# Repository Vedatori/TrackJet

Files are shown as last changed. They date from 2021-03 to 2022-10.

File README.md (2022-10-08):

# TrackJet (cz)
TrackJet je otevřená platforma robotického vozidla vyvinutá pro [Robotický tábor 2021](http://wp.vedatori.com/pobytove-tabory/) organizovaný spolkem [Vědátoři](http://wp.vedatori.com/). Jedná se o nástupní verzi vozidla [TrackRay](https://github.com/vedatori/TrackRay), ve které byly vylepšeny jeho terénní schopnosti a přidány nové funkcionality. Byla redesignována mehanická konstrukce i řídicí elektronika, pro kterou byl vyvinut odpovídající software. 

Hlavní mechanickou částí je 3D tištěné šasi, které je doplněno dalšími 3D tištěnými díly. Plošné díly jsou laserem vyřezány z překližky. Spojování je prováděno především šrouby M3. Je použito minimum lepených spojů tak, aby bylo možné vrátit jakýkoliv krok při stavbě. Obsahuje zadní pohonná kola a na každé straně dále tři kola pro vedení pásu. Všechna kola jsou uložena pevně. Pásy jsou vytištěny na 3D tiskárně tak, aby se již při tisku vytvořilo kloubové spojení jednotlivých segmentů, což vede ke snížení času potřebného pro stavbu.

Veškerá elektronika je umístěna na jedné DPS. Ze spodní strany je připevněn zdroj energie - akumulátor 18650. Jeho nabíjení je řešeno na DPS, pro nabití není nutné ho vyjmout. Robota řídí ESP32 připájené přímo do DPS. Pro orientaci v prostoru robot využívá snímání pohybu pásů pomocí optických enkodérů a senzoru LiDAR umístěného na otočné konzoli. Vstupy od uživatele je možné zadat pomocí rotačního enkodéru, potenciometru a tlačítka, výstupy jsou zobrazeny na LED matici, bzučákem nebo jiných LED. Programování a nabíjení robota je prováděno přes USB-C.

Software je připraven na výuku programování. Tomu je přizpůsobena knihovna, pomocí které uživatelé jednoduše ovládají periferie robota bez nutnosti nízkoúrovňového programování jednotlivých částí. Pro výuku programování je připraven také návod popisující jednotlivé funkce a příklady jejich použití. Vše bylo navrženo s důrazem na rozvoj schopností algoritmizace a programování účastníků.
Součástí softwarového balíku je i kompletní program pro dálkové ovládání přes WiFi. Vozidlo umožňuje komunikaci jak přes vlastní WiFi, tak přihlášení k již existující síti. To mu umožňuje jízdu i v širém prostoru. TrackJet můžete vidět v akci v [tomto videu](https://www.youtube.com/watch?v=zHig3jCnhBY).

Při stavbě TrackJet postupujte podle připravených návodů v následujícím pořadí:
1. [Návod pro mechaniku](https://github.com/vedatori/TrackJet/blob/main/Manuals/TrackJet_mechanics_cz.md)
1. [Návod pro elektroniku](https://github.com/vedatori/TrackJet/blob/main/Manuals/TrackJet_electronics_cz.md)
1. [Návod pro programování](https://github.com/vedatori/TrackJet/blob/main/Manuals/TrackJet_programming_cz.md)

## Licence
* Obsah tohoto repozitáře mimo složku *Software* je sdílen pod licencí [Attribution-NonCommercial-ShareAlike 4.0 International (CC BY-NC-SA 4.0)](https://creativecommons.org/licenses/by-nc-sa/4.0/).
* Obsah složky *Software* je sdílen pod licencí [GNU Lesser General Public License v3.0](https://www.gnu.org/licenses/lgpl-3.0.en.html).

# TrackJet (en)

TrackJet is an open-source robotic vehicle platform developed for the [Robotic camp 2021 (cz)](http://wp.vedatori.com/pobytove-tabory/) organized by [Vědátoři (cz)](http://wp.vedatori.com/) society. It is a succesor of [TrackRay](https://github.com/vedatori/TrackRay) robotic vehicle. TrackJet introduces enhanced terrain abilities and new functionalities. Mechanical parts, electronics and software were redesigned.

TrackJet consists of a main 3D printed part - chassis, several other 3D printed parts and laser cut plywood parts. M3 bolts are used in the assembly process, which grants the possibility to undo every step in case of assembly error. Rear propulsion wheel and three guiding wheels are placed on every side of the vehicle. Tracks are designed to be 3D printed in one piece with joints between segments which minimizes assembly time.

All electronic components are placed on a single PCB. This board contains 18650 battery and a charger circuit. Therefore, it is not needed to take the battery out in order to charge it. ESP32 soldered to the PCB is used for peripherals control and WiFi connectivity. TrackJet finds its orientation in space using LiDAR sensor and optical encoders. User inputs can be made using rotary encoder, potentiometer and a button. LED matrix, buzzer and other LEDs are used for communication with user. Vehicle is programmed and charged via USB-C.

Electronics and software is designed for programming education. TrackJet contains a library which allows easy peripherals control without the need of low-level programming abilities. Repository contains programming manual (in czcech language) with description of commands and examples. WiFi remote control is a part of the software pack in this repository. ESP32 can be connected to external WiFi or it can create its own network so it is possible to drive outdoors without network coverage. You can see TrackJet in action in [this video](https://www.youtube.com/watch?v=zHig3jCnhBY).

In the build of the TrackJet proceed according to the prepared manuals in the following order:
1. [Mechanics manual](https://github.com/vedatori/TrackJet/blob/main/Manuals/TrackJet_mechanics_cz.md)
1. [Electronics manual](https://github.com/vedatori/TrackJet/blob/main/Manuals/TrackJet_electronics_cz.md)
1. [Programming manual](https://github.com/vedatori/TrackJet/blob/main/Manuals/TrackJet_programming_cz.md)

## License
* The contents of this repository excluding folder *Software* is shared under license [Attribution-NonCommercial-ShareAlike 4.0 International (CC BY-NC-SA 4.0)](https://creativecommons.org/licenses/by-nc-sa/4.0/).
* The contents of the folder *Software* is shared under license [GNU Lesser General Public License v3.0](https://www.gnu.org/licenses/lgpl-3.0.en.html).


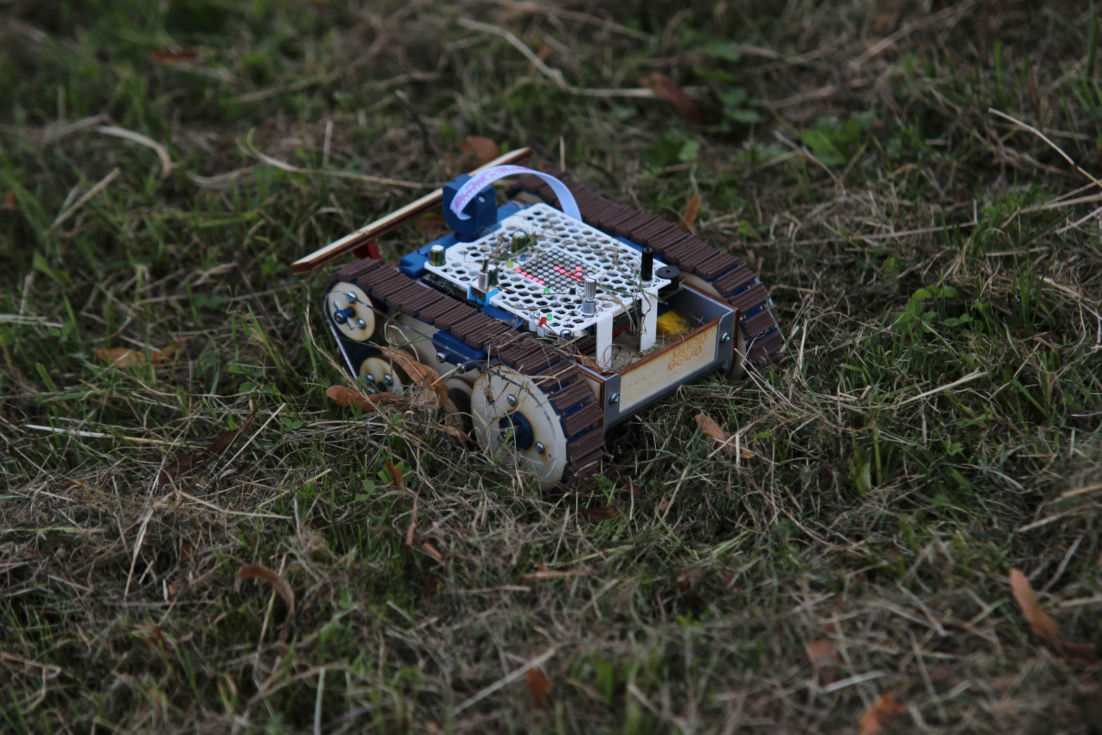
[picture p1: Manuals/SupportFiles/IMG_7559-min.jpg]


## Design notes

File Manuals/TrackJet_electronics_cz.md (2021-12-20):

V tomto dokumentu je uveden návod na osazení desky plošných spojů. Některé součástky byly osazeny strojově při výrobě desek. Zbytek osazení je předmětem tohoto návodu.
Pro tento návod si uvedeme následující pojmy: 
* DPS (Deska Plošných Spojů) - Placatá věc, na kterou budeme nyní pájet součástky a které jsou skrze ni elektricky pospojované.
* PCB (Printed Circuit Board) - To stejné, co DPS.
* SMD (Surface Mount Device) - Tzv. bezvývodové elektronické součástky, které mají krátké nožičky. Tyto součástky jsou připájeny k DPS pouze z jedné strany. Tyto součástky byly osazevy strojově při výrobě DPS.
* THT (Through-hole Technology) - Tzv. vývodové elekotronické součástky, které mají dlouhé nožičky. Tyto nožičky jsou před zapájením součástky prostrčeny skrz díry v DPS.

THT součástky budeme v následujících krocích pájet následujícím způsobem:
1. Součástku vkládáme ze strany, kde je naznačena silkscreenem (kde je bílou barvou natištěn její obrys).
1. Součástku přitlačíme až k desce nebo co nejblíž.
1. Součástku pájíme ze strany, na kterou trčí vývody.
1. Vývody po zapájení zastřihneme.

# Obsah
* [Pájení senzorů pohybu](#LED1)
* [Pájení LED](#LED2)
* [Pájení malých součástek](#male)
* [Pájení větších součástek](#vetsi)
* [Pájení konektorů a senzorů čáry](#konektory)
* [Zakrytování PCB, propojení periferií](#finalizace1)
* [LIDAR](#finalizace2)
* [LIDAR2](#finalizace3)

## <a name = LED1>Pájení senzorů pohybu</a>
**Potřebujeme:**
* kleště
* 4x modul s LED a fotodiodou
* 2x plastový držák pro modul z 3D tiskárny
* 2x plastový vymezovač z 3D tiskárny
* 2x šroub M3x8 

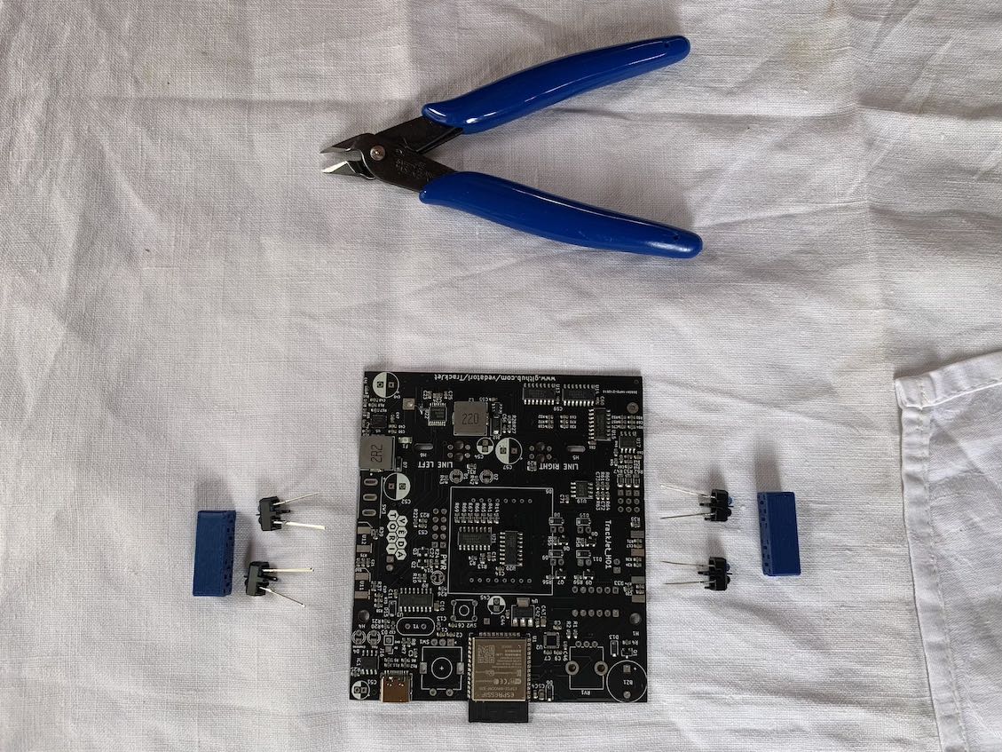
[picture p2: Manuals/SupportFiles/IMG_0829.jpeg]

**Postup:**
1. Vložte postupně moduly do držáku z 3D tiskárny. *Je třeba dodržet orientaci diod s obrázkem pro jednotlivé strany. Modrá čára na schématu označuje pozici "nosu" na součástce.* Barvu diod je možné rozpoznat pod světlem např. z LED telefonu.
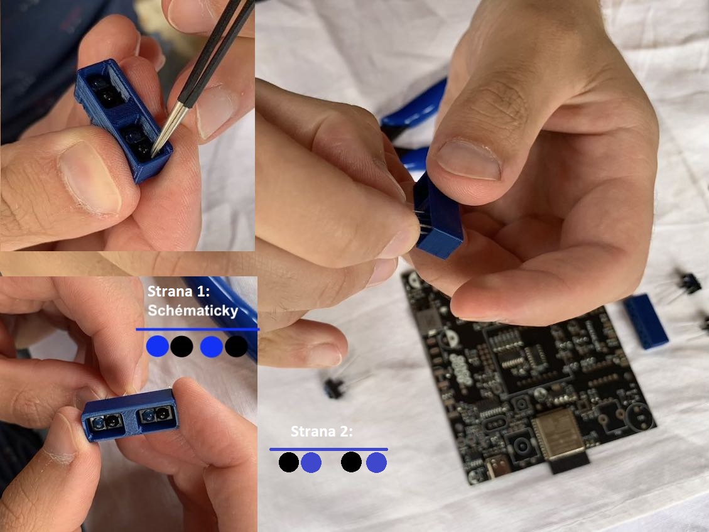
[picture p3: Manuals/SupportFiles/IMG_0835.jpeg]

1. Vývody musí být protažené dvěma podélnýma dírama v 3D tisknutém díle (ne těmi v rozích).
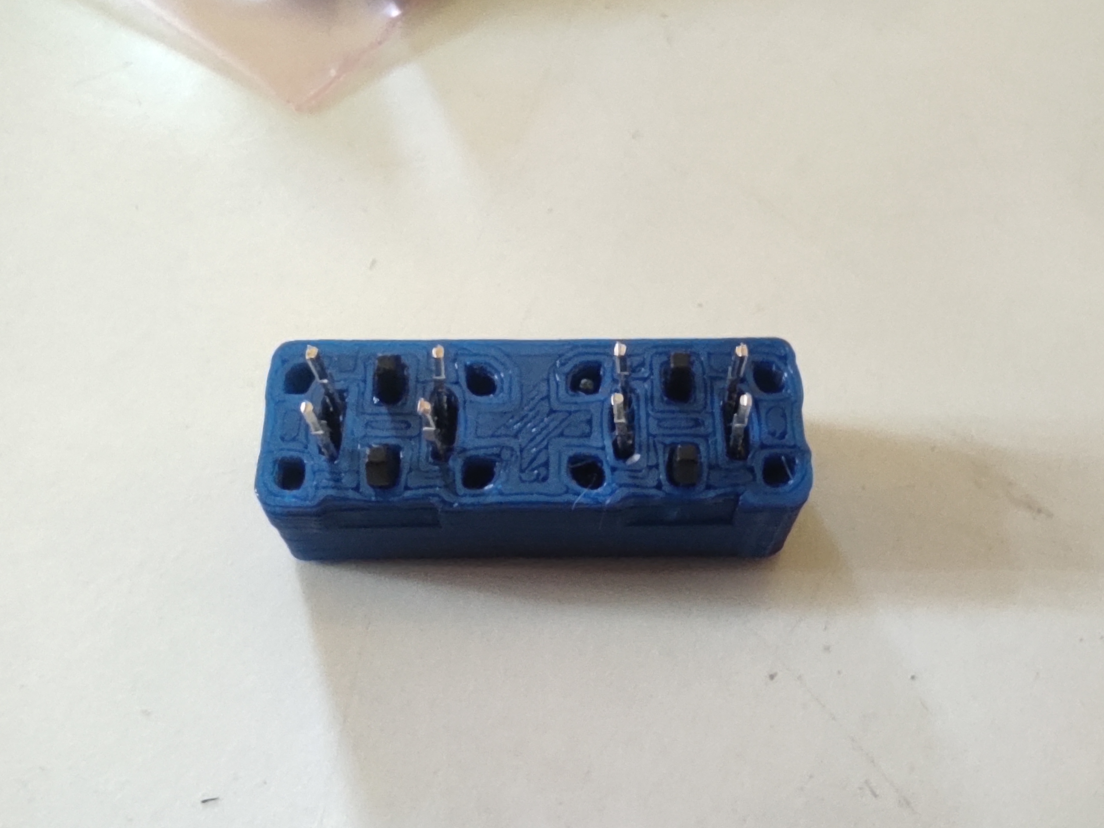
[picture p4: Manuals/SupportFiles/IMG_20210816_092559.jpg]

1. Opakujte postup pro druhou stranu 2 podle schématu. Zarovnejte nožičky podle obrázku, aby obejmuly shora a zespodu PCB a směřovali doprostřed pájecí plochy. *Nos na součástce je nahoře.*
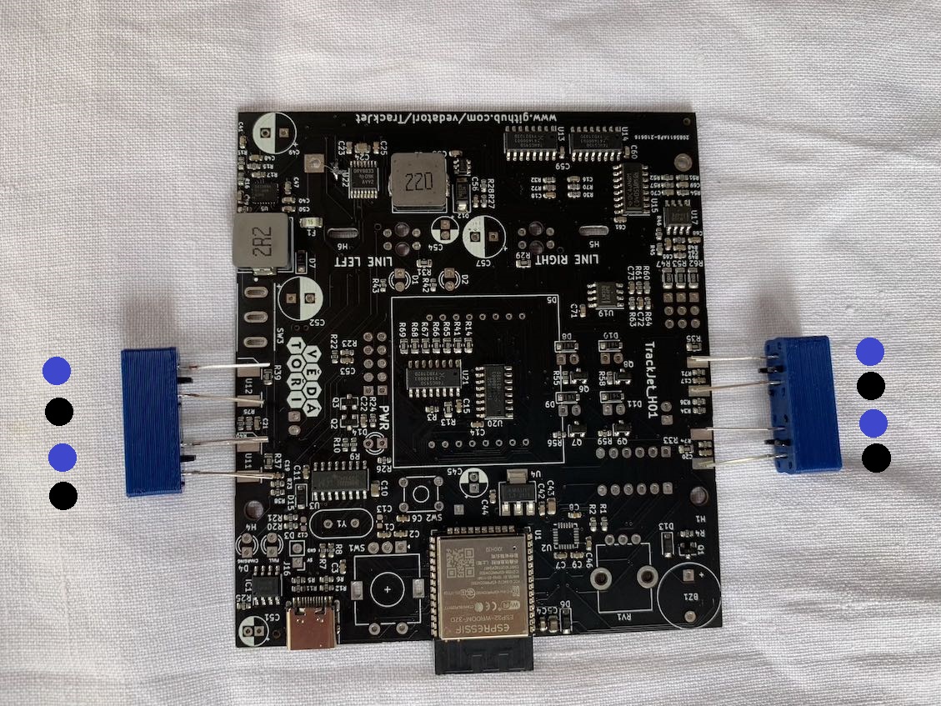
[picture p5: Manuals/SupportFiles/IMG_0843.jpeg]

1. Použijte zarovnávací nástroj z 3D tiskárny, umístěte do něj moduly podle obrázku. Na vyznačené červené čáře zakraťte vývody kleštěmi.
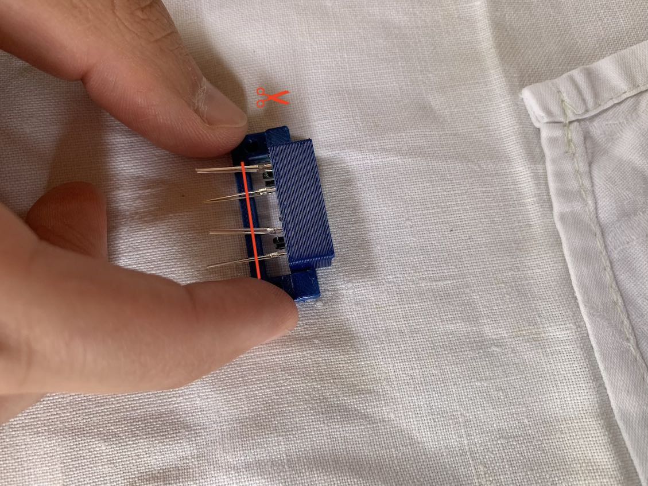
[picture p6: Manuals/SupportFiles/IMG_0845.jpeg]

1. Zarovnávací nástroj z 3D tiskárny umístěte pod PCB a přišroubujte šroubkem.
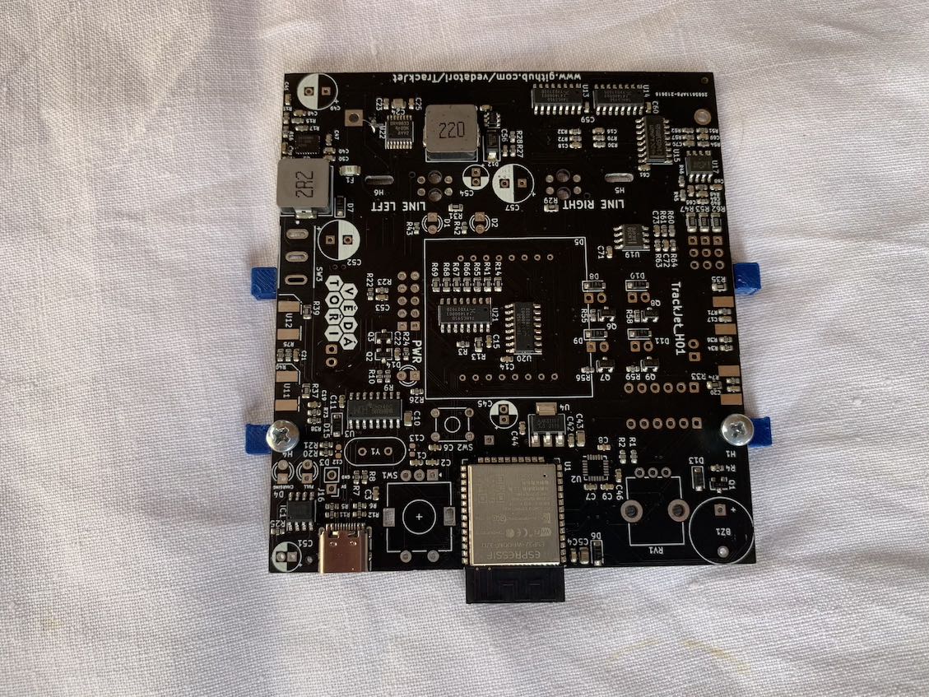
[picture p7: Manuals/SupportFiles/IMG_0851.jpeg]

1. Zarovnejte nožičky podle obrázku, aby obejmuly shora a zespodu PCB a směřovaly doprostřed pájecí plochy. *Modul z 3D tiskárny musí přiléhat k PCB bez mezery.*
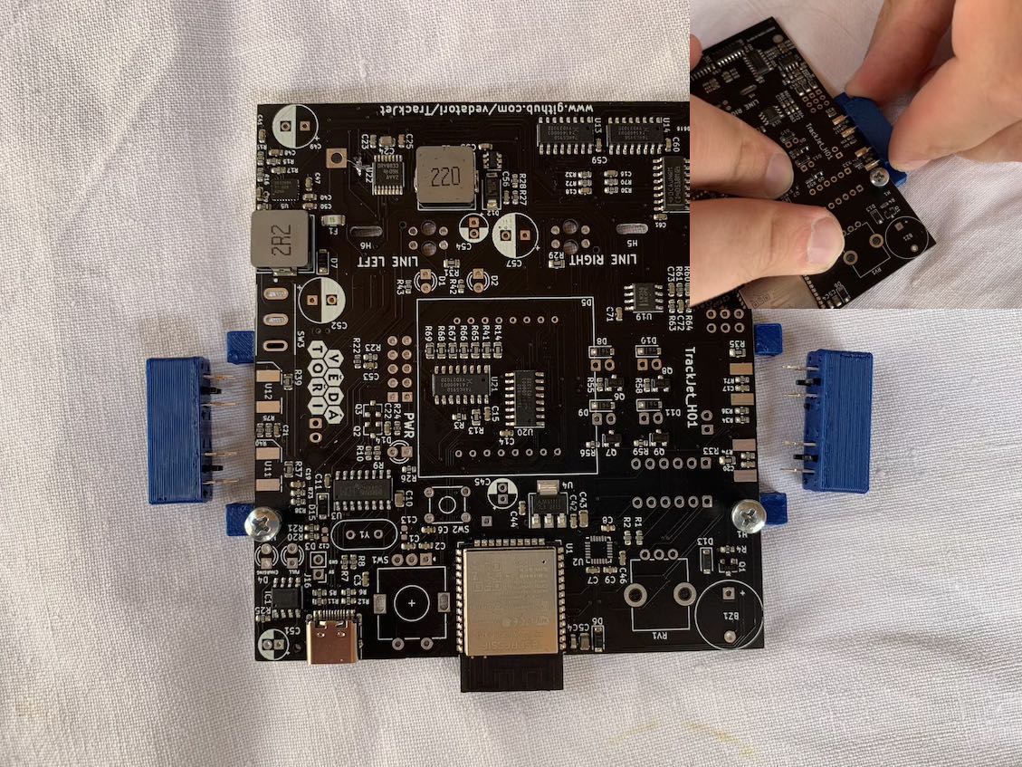
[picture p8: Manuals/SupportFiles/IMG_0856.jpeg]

1. *Zapájejte z horní strany PCB.*
1. Vyšroubujte díl pro zarovnání z 3D tiskárny. 
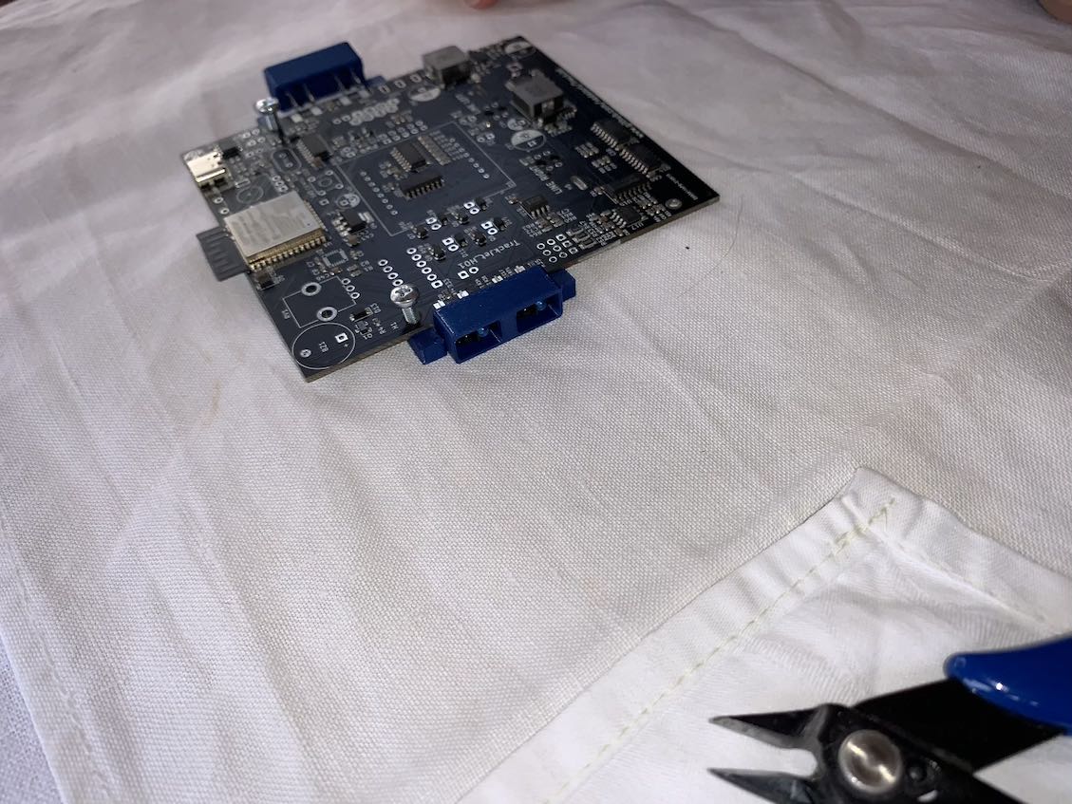
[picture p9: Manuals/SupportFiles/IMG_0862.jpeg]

1. Otočte na druhou stranu, vyrovnejte nožičky na střed pájecí plochy. Zapájejte.
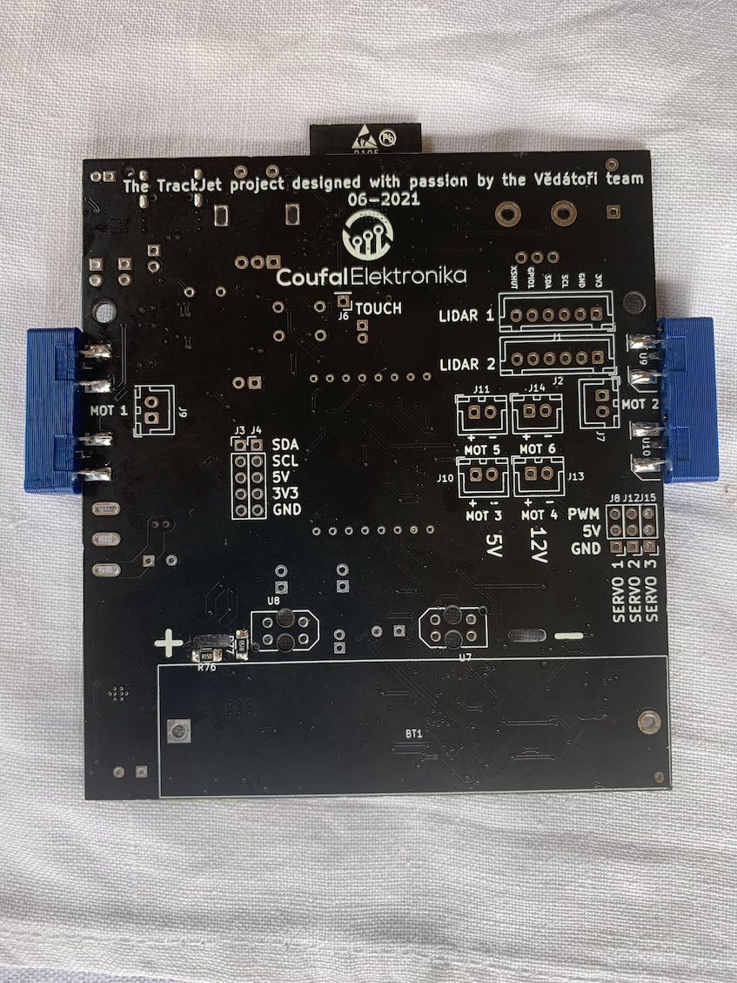
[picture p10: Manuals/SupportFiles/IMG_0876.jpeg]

1. Otestujte, zda PCB padne do šasi. *Při usazování netlačte. Pokud deska nezapadne hladce, zavolejte vedoucího.*
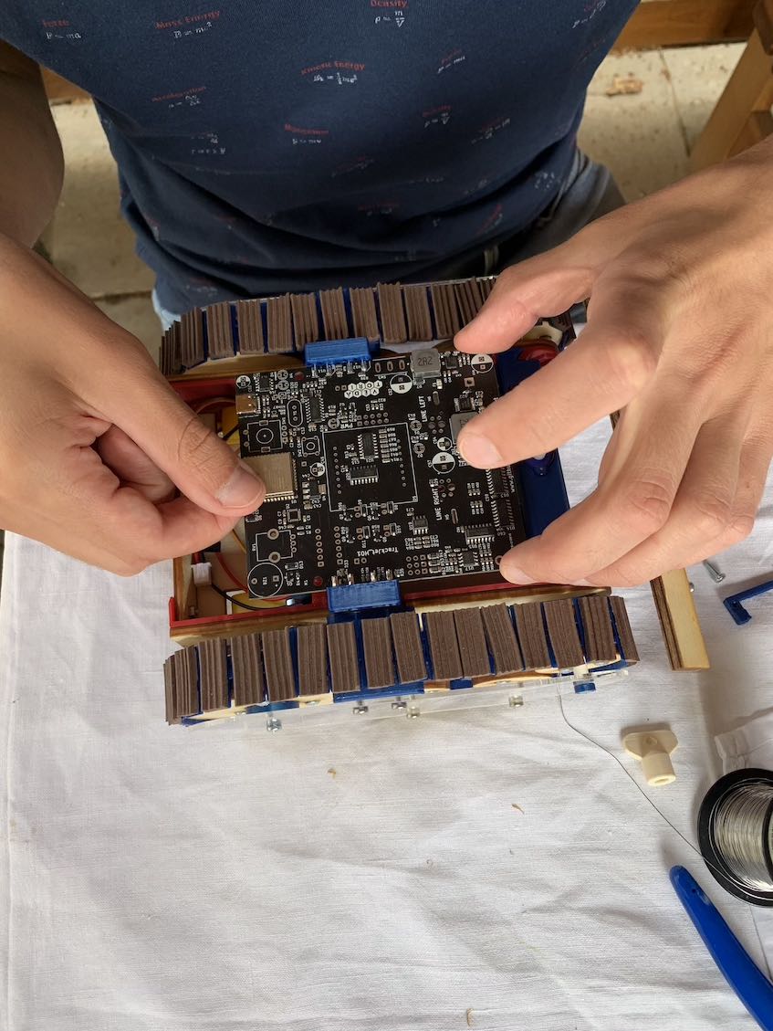
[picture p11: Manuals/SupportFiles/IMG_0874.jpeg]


## <a name = LED2>Pájení LED</a>
**Potřebujeme:**
* kleště
* 2x zelená LED
* 1x červená LED
* 2x LED oblíbené barvy vlastního výběru
* 5x distanční sloupek pro LED

**Postup:**
<span style="color: red;">**POZOR: LED mají definovanou polaritu!**</span> U každé LED zkontrolujte, že kratší nožku vsouváte do čtveraté díry! 
1. Na každou LED navlékněte distanční sloupek. Použijte ty bílé, které máte v sáčku s mechanikou
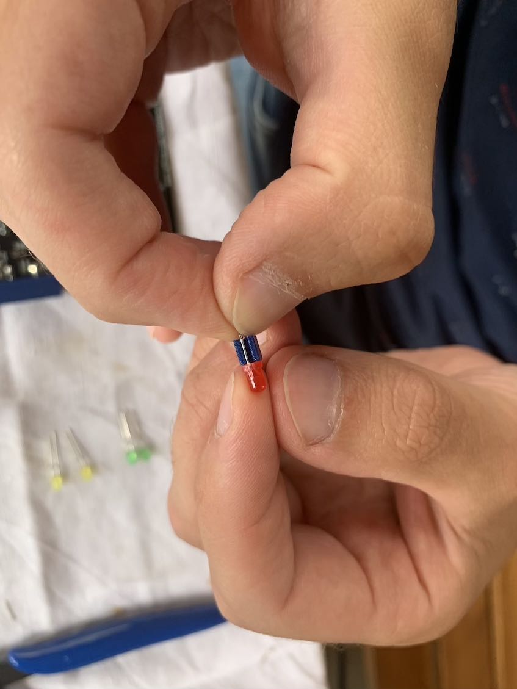
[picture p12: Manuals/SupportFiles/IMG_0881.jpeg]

1. Provlékněte červenou LED místem označeným D4 CHARGING. Zahněte nožičky natěsno u PCB. Cín se nanáší ze strany s logem Coufal Elektronika. Zapájejte.
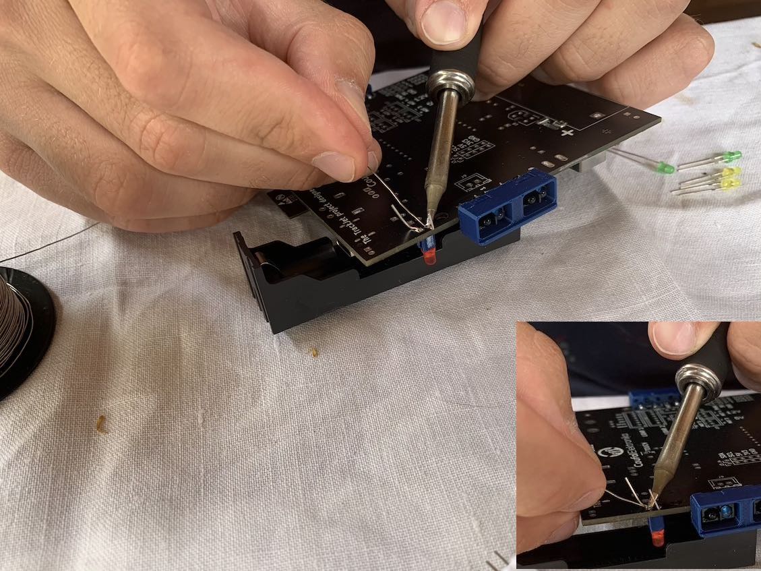
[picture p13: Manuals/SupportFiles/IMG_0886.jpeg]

1. Provlékněte zelenou LED místem označeným D3 FULL. Opakujte stejný postup pájení jako v předchozím kroku.
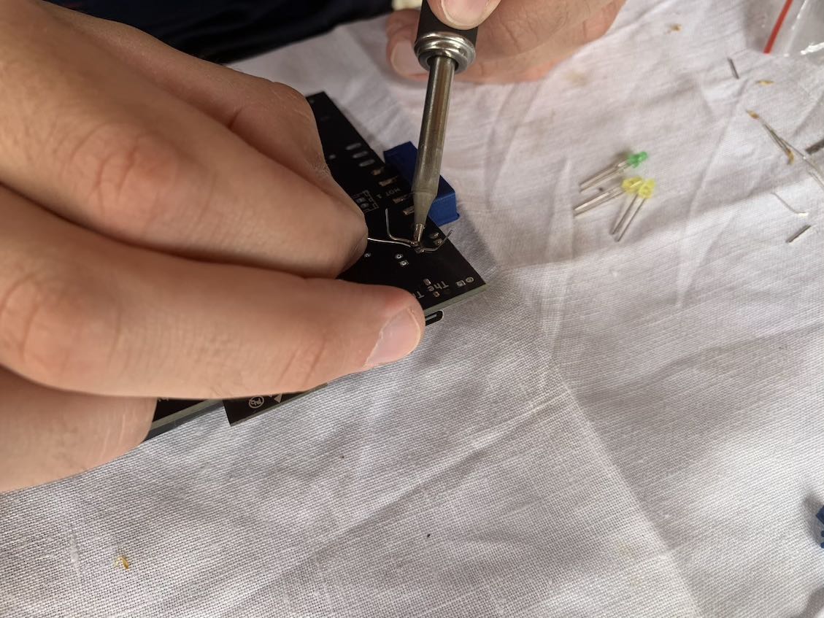
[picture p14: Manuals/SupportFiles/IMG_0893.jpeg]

1. Zastřihněte nožičky u PCB. *Stříhanou nožičku držte rukou, aby neodletěla sousedovi do oka.*
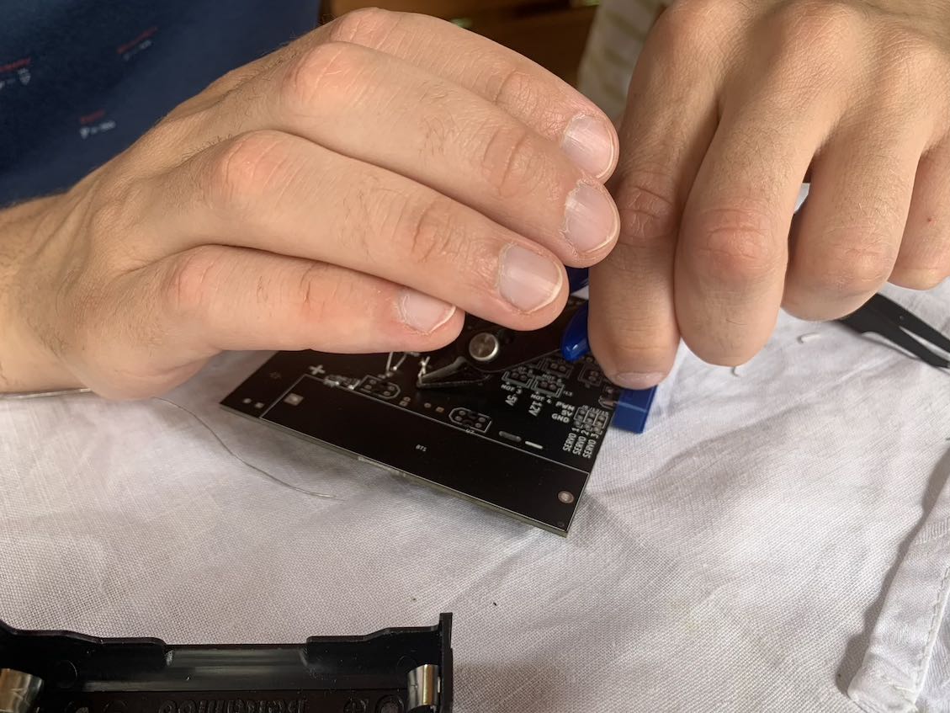
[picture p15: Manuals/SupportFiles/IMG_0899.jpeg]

1. Obdobným postupem zapájejte zelenou LED místem ozančeným D14 a vybrané LED místy označenými D1 a D2.


## <a name = male>Pájení malých součástek</a>
**Potřebujeme:**
* kleště
* bzučák
* 3x elektrolytický kondenzátor 100 µF (menší pouzdro)
* 3x elektrolytický kondenzátor 1000 µF (větší pouzdro)

**Postup:** 
1. Zapájejte buzzer do levého horního rohu. Pozor na polaritu, delší vývod (u symbolu plus na plastovém pouzdře buzzeru) musí být umístěn do otvoru označeným symbolem +. Buzzer mírně nesedí tak, jak by měl, proto je potřeba jeho vývody mírně rozevřít od sebe.
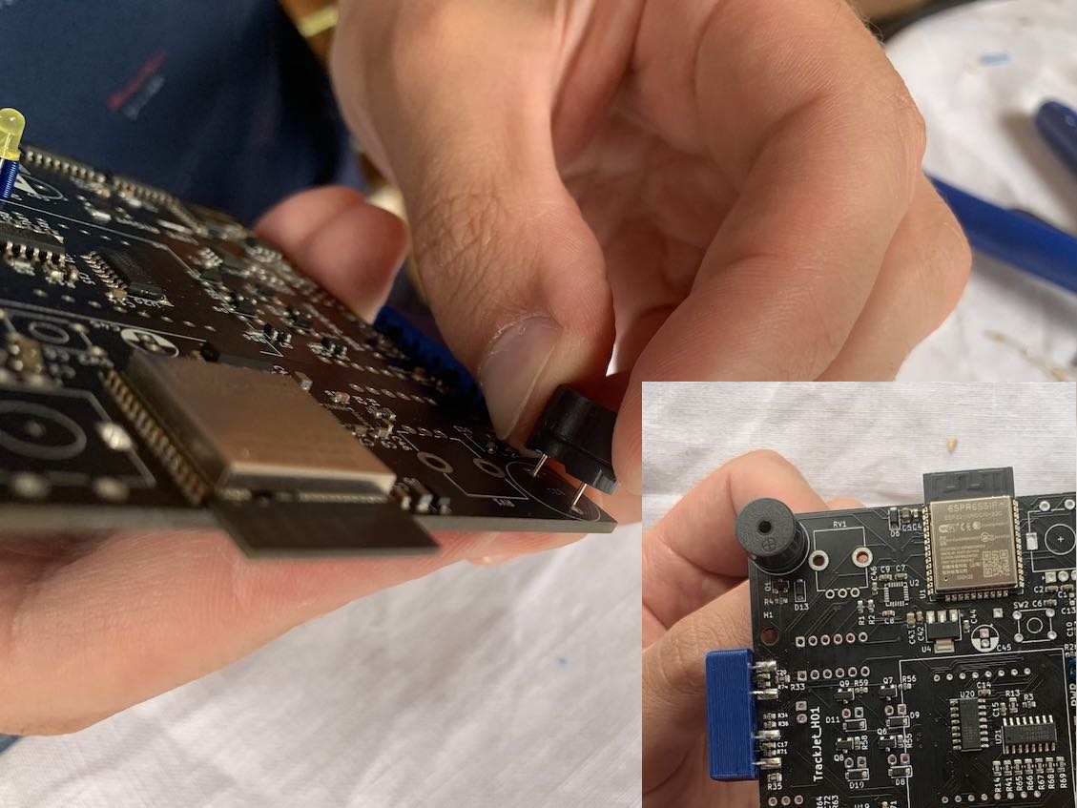
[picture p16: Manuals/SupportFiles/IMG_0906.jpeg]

1. Na místa označená C51, C54 a C45 zapájejte elektolytické kondenzátory 100 µF. Pozor na polaritu, delší vývod musí směřovat do otvoru, u kterého je smybol + a jeho okolí není zabarvené bílou barvou. 
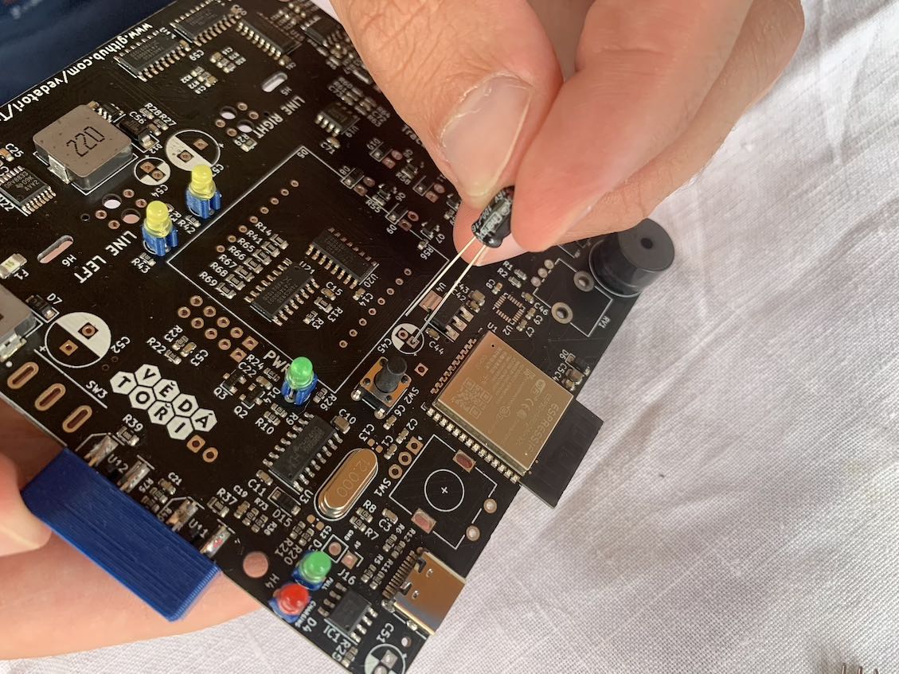
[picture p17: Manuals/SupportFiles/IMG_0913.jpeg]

1. Na místa označená C49, C52 a C57 zapájejte elektolytické kondenzátory 1000 µF. Pozor na polaritu, delší vývod musí směřovat do otvoru, u kterého je smybol + a jeho okolí není zabarvené bílou barvou. 
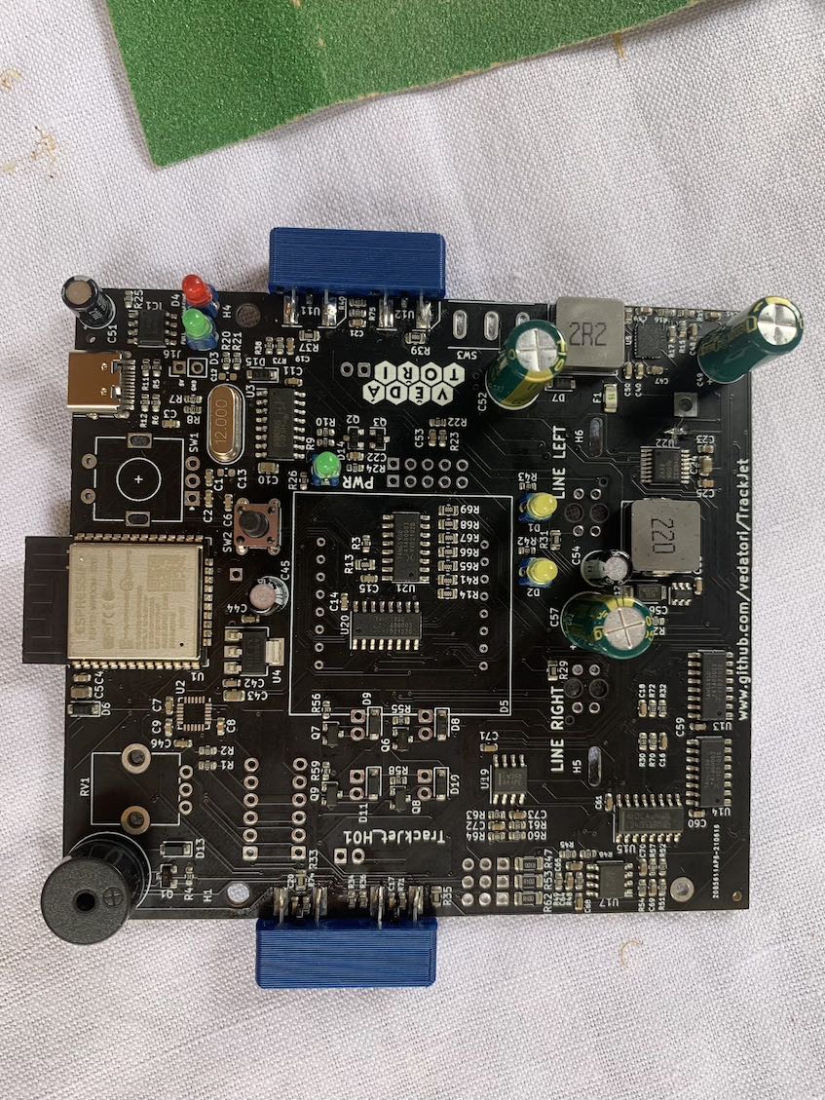
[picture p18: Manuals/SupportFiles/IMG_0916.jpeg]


## <a name = vetsi>Pájení větších součástek</a>
**Potřebujeme:**
* kleště
* přepnínač
* rotační enkodér
* ponteciometr
* matice LED
* tlačítko

**Postup:** 
1. Zapájejte přepínač na místo označené SW3.
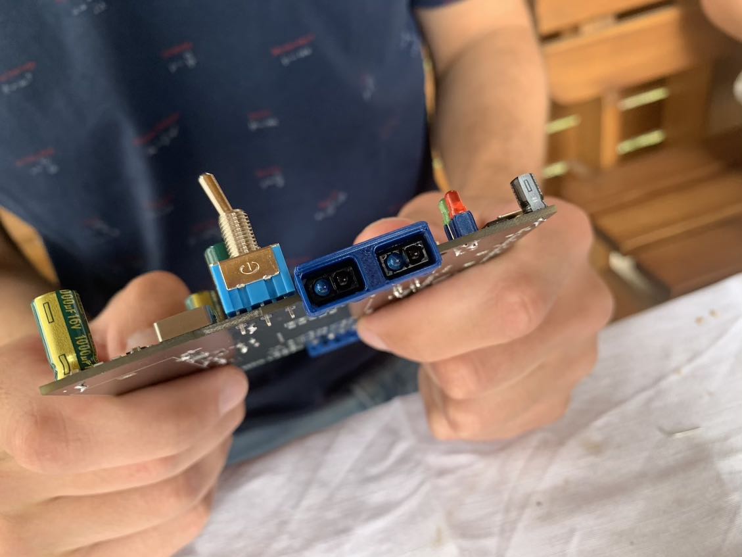
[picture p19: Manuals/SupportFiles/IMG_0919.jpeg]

1. Zapájejte enkodér na místo označené SW1. *Nejprve připájejte kontakty po bocích, poté 3 vývody ze spodní strany. Zkontrolujte, že je enkodér přitlačený k desce a osa čouhá kolmo na desku.*
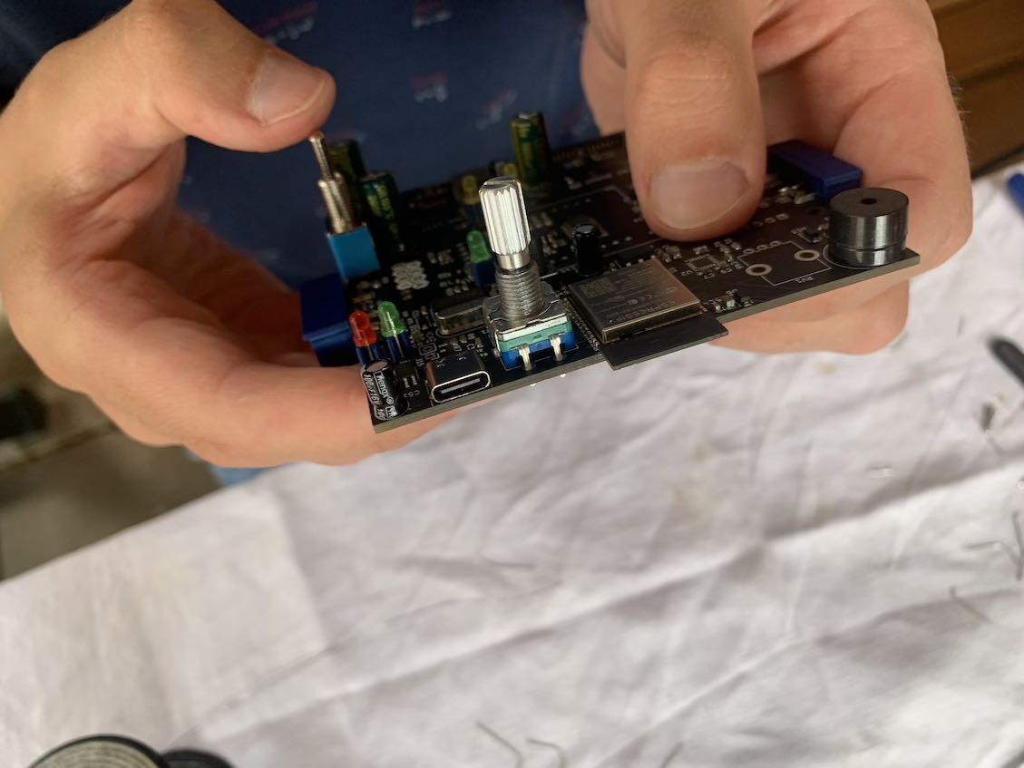
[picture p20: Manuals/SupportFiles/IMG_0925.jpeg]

1. Zapájejte potenciometr na místo označené RV1. *Nejprve připájejte kontakty po bocích, poté 3 vývody ze spodní strany. Zkontrolujte, že je potenciometr přitlačený k desce a osa čouhá kolmo na desku.*
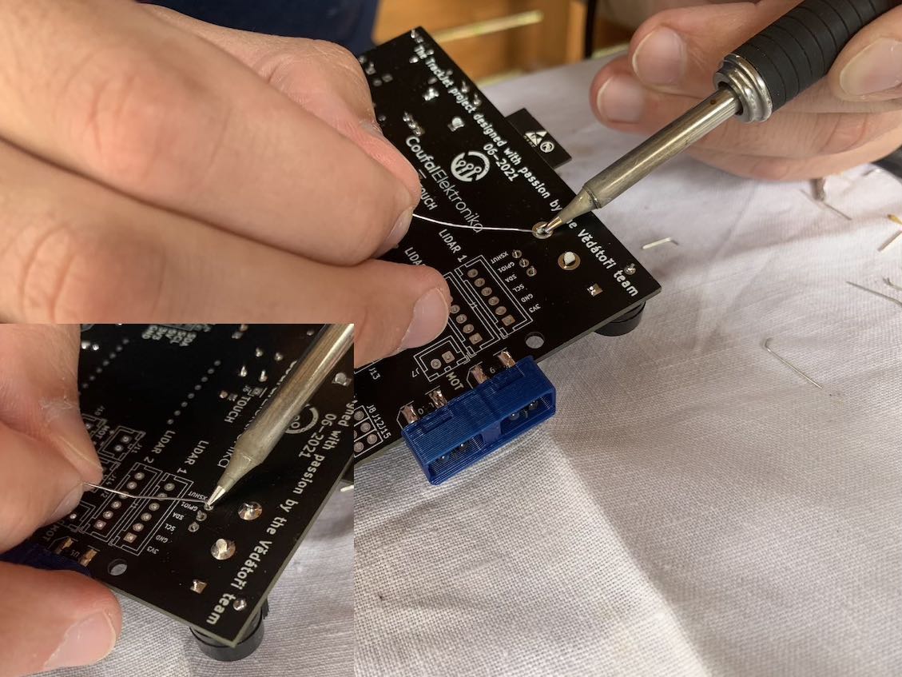
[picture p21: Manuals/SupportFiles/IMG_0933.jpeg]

1. Vložte matici LEDek do PCB. Kód na horní straně musí být blíž k čipu s nápisem Espressif, aby byla zachována polarita, viz obrázek.
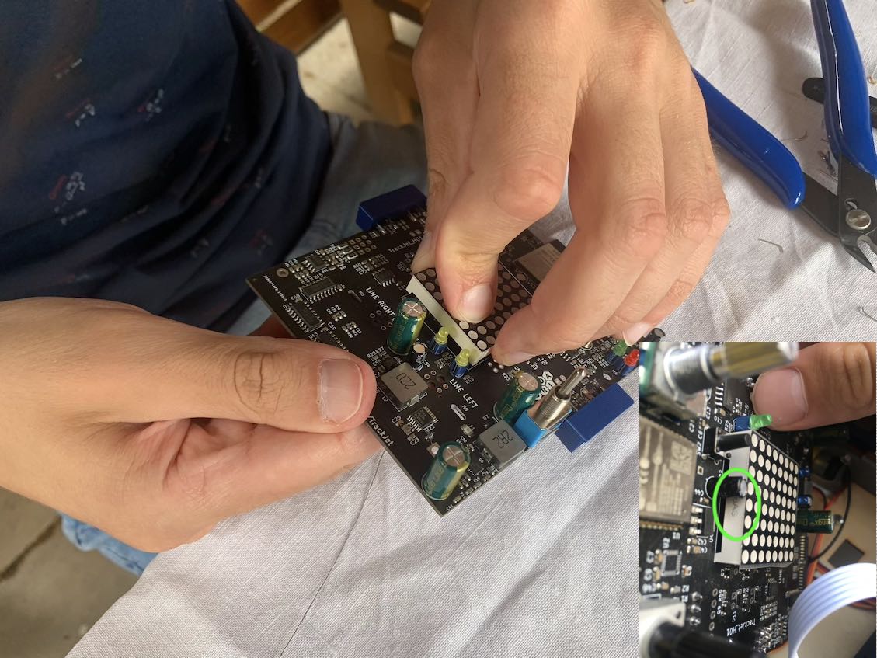
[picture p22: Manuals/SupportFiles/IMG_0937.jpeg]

1. Zahněte pomocí kleští krajní nožičky, aby matice nevypadávala při pájení z desky. Zavolejte vedoucího na kontrolu polarity, oprava špatně otočeného matrixu je téměř neproveditelná!
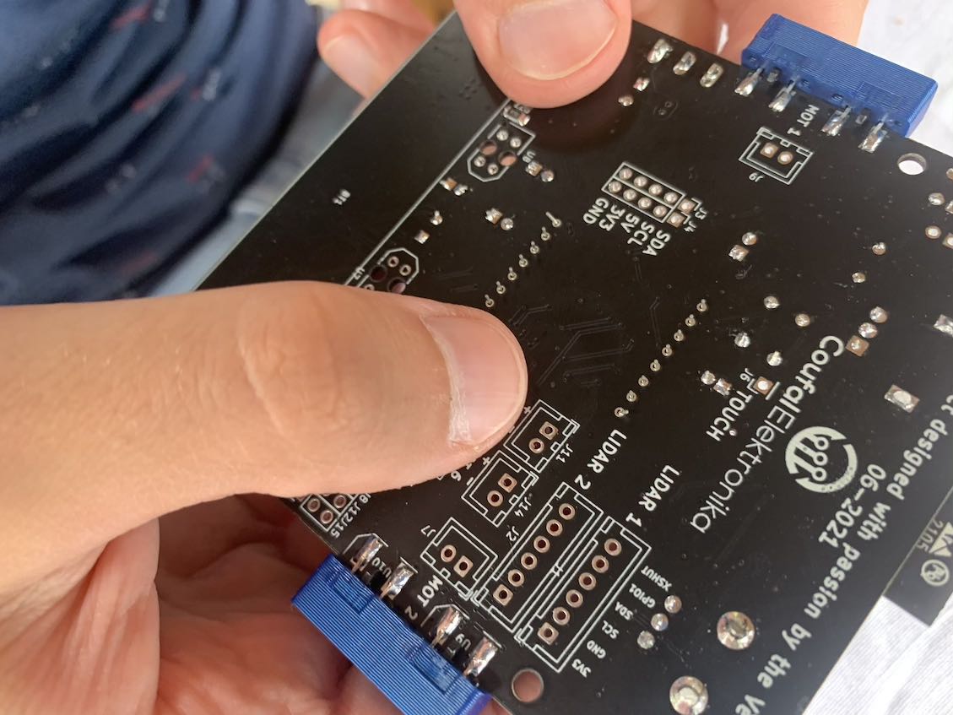
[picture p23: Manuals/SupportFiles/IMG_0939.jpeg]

1. Zapájejte matici LEDek. Na závěr zapájejte tlačítko do místa označeného SW2.
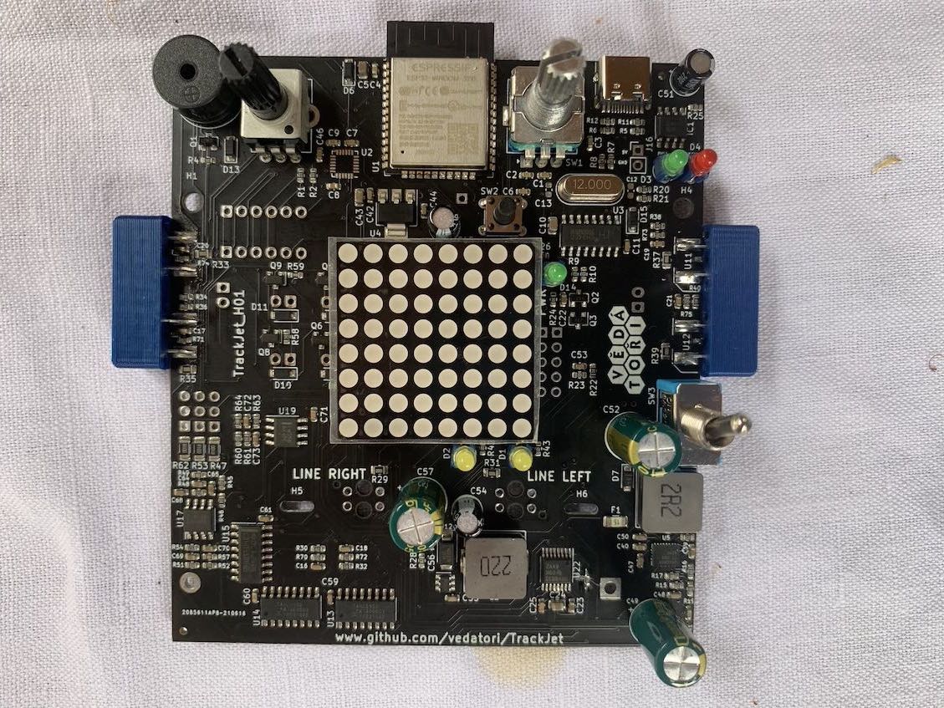
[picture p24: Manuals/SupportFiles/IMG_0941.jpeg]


## <a name = konektory>Pájení konektorů a senzorů čáry</a>
**Potřebujeme:**
* kleště
* 2x konektor se 2 piny
* 1x konektor se 6 piny
* 3x kolíková lišta se třemi konektory
* 2x modul s diodami
* 2x podpěry modulu s diodami z 3D tiskárny
* držák baterie

**Postup:** 
1. Zapájejte kolíkové lišty do míst označených SERVO 1, SERVO 2, SERVO 3. Vytvořte libovolnou barevnou kombinaci. *Kolíková lišta musí být vždy rovnoběžně s nápisy SERVO.*
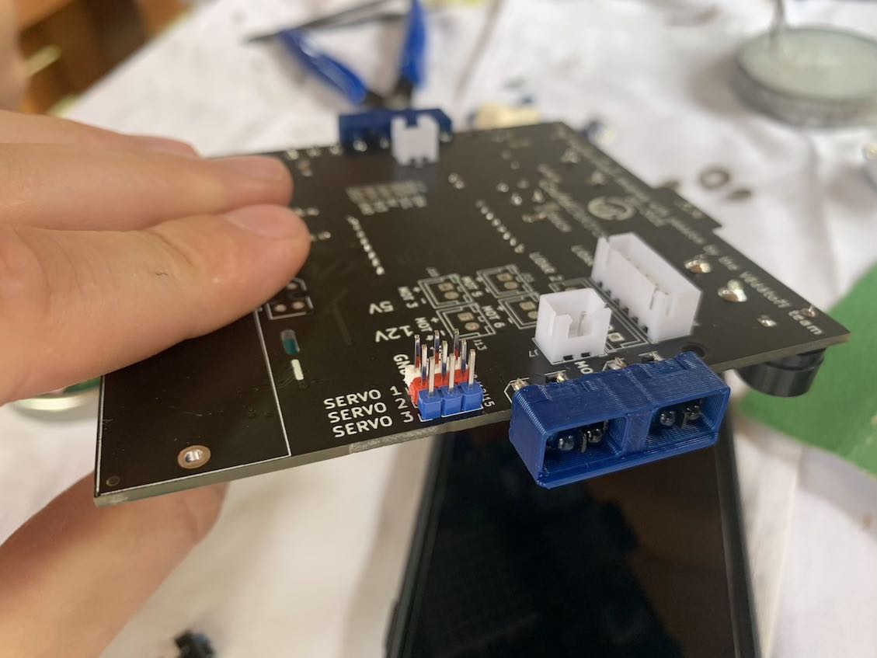
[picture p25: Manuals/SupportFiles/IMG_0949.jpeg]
 
1. Zapájejte lišty konektorů do míst LIDAR1, J6 a J7. Polarita je vždy zřejmá z nákresu na PCB.

1. Provlečete modul s diodami podpěrou. *Veškerá zkosení modulu jsou i na podpěře a musí lícovat. Z jedné strany podpěry je výřez pro kolík vystupující ze součástky.*

1. Připájejte moduly s podpěrou na místa označená U7 a U8. Polarita je zřejmá z nákresu na PCB.

1. Zapájejte držák baterie. Důsledně zkontrolujte polaritu.

1. Překontrolujte desku zepředu.

1. Překontrolujte desku zezadu.


**Nechte desku překontrolovat vedoucím. Nechte si od něj vložit baterku.**

## <a name = finalizace1>Zakrytování PCB, propojení periferií</a>
**Potřebujeme:**
* kryt desky z 3D tiskárny ve tvaru plástve
* 2x stahovací páska
* oboustranná lepicí páska
* kleště

**Postup:**
1. Přichyťte baterku a kryt k PCB pomocí velkých upínacích pásků (volitelné), jejich konce zastřihněte kleštěmi. Pásky protahujte díryami H5 a H6 v desce. Hlavy upínacích pásků dejte do stejné pozice, jako vidíte na obrázku.


1. Konce pásků zastřihněte kleštěmi.

1. Konce pásků zastřihněte kleštěmi.

1. Vystřihněte kousek oboustranné lepicí pásky. Vlepte jej do prostoru mezi otvory pro senzory čáry.

1. Zachyťe kabely od servomotorů na pásku.

1. Zastrčte konektory motoru do desky, jak je naznačeno na obrázku.

1. Připojte vývody od servo motoru na kolíkovou lištu. Výstup SERVO 1 je určen pro radlici. Výstup SERVO 2 je určen pro LIDAR.


## <a name = finalizace2>LIDAR</a>
**Potřebujeme:**
* LIDAR



**Postup:**
1. Připojte vývod LIDARu na konektor LIDAR. Kabel proveďte okolo PCB stejně jako na obrázku.

1. Přišroubujte desku pomocí sřoubů k šasi.


## <a name = finalizace3>LIDAR 2</a>
**Potřebujeme:**
* vrut z balení k servomotoru
* 2x vrut 2,2x10



**Postup:**
1. *Vytočte servo motor na maximum doleva.* Nasaďte na servomotor držák v úhlu 90° vůči šasi.

1. Přišroubujte držák pomocí vrutu z balení k servomotoru.

1. Vložte LIDAR a zašroubujte kryt.

1. Výsledná podoba.


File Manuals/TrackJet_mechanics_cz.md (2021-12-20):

V tomto dokumentu je uveden návod na sestavení mechanických dílů vozítka TrackJet. Část mechanických dílů je vyrobena technologií 3D tisku, část je vyřezána z překližky a plexiskla pomocí laseru. Ostatní součástky jsou běžně dostupný spojovací materiál. Dále je vsazena deska plošných spojů (DPS), kterou se zabývá samostatný návod.

___
# Obsah
* [Příprava překližkových dílů](#preklizka)
* [Sestavení velkých kol](#kolo)
* [Sestavení malých kol](#kolecka)
* [Příprava bočnic #1](#bocnice1)
* [Příprava držáků motorů](#drzaky)
* [Sestavení bočnic](#bocnice2)
* [Nasazení kol](#kola)
* [Kompletace šasi #1](#sasi1)
* [Příprava bočnic #2](#bocnice3)
* [Kompletace šasi #2](#sasi2)
* [Držák servo motoru](#serva)
* [Sestavení radlice](#radlice)
* [Polepení pásů](#pasy1)
* [Slepení pásů](#pasy2)
* [Nasazení pásů](#pasy3)
___

## <a name = preklizka>Příprava překližkových dílů</a>
**Potřebné díly:**
* všechny díly z překližky

**Nástroje:**
* smirek



**Postup:**
1. Obruste smirkem všechny nedořezky.
    

## <a name = kolo>Sestavení velkých kol</a>
**Potřebné díly:**

* 2x kolo neozubené velké z překližky
* 1x kolo ozubené velké z překližky
* 1x kolo ozubené velké 3D tisk
* 3x matka M3
* 3x šroub M3x20

**Nástroje:**
* křížový šroubovák
* maticový klíč



**Postup:**
1. Pořadí navlékání. 
    
1. Provléct šroub skrz díru pod malou dírkou ve velkém kole z překližky. Hlava šroubu zapadne do zahloubení. Navléct ozubené kolo z překližky. *Malé dírky musí padnout na sebe.*
    
1. Navléct 3D tištěný díl tak, aby výstupek pro zastrčení osy směřoval směrem od dřevěných dílů. *Malé dírky musí opět padnout na sebe.*
    
1. Navléct neozubené velké kolo z překližky. Zašroubovat matku. Neutahovat.
    
1. Doplnit zbylé šrouby a matky.
    
1. Díly vystředit vůči sobě. Všechny matky utáhnout (přitlačit prstem do zahloubení nebo použít maticový klíč, pokud při přitlačení prstem prokluzují). 
    
1. Celý postup zopakovat pro druhé kolo.

## <a name = kolecka>Sestavení malých kol</a>
**Potřebné díly:**

* 2x malé kolo neozubené z překližky
* 2x maličké kolo neozubené z překližky
* 1x vymezovač kola 3D tisk
* 3x matka M3
* 3x šroub M3x20


**Nástroje:**
* křížový šroubovák
* maticový klíč

**Postup:**
1. Provléct šroub skrz malé kolo. Provléct vymezovač do díry v prostřed kola tak, aby jeho tenká část trčela směrem od strany, kde je zahloubení.
    
1. Hlava šroubu musí zapadnout do zahloubení.
    
1. Navléct 2 maličké kolečka a jedno velké. 
    
1. Zašroubovat matičku do zahloubení, neutahovat.
    
1. Doplnit zbylé šrouby a matky. Díly vystředit vůči sobě. Všechny matky utáhnout. 
    
1. Stejným postupem sestavit zbylá kola. Celkově jich bude 6. 
    

## <a name = bocnice1>Příprava bočnic</a>
**Potřebné díly:**
* 1x šasi z 3D tiskárny
* 2x matka M3

**Nástroje:**
* štípací kleště
* ploché kleště


**Postup:**
1. Vystříhat přebytečné podpory 3D tisku. 
    
1. Výsledný vzhled. 
    
1. Vložit matky do přpravených otvorů z vnější strany šasi. Zatlačit plochými kleštěmi. 
    

## <a name = drzaky>Příprava držáků motorů</a>
**Potřebné díly:**
* 2x držák motoru z 3D tiskárny
* 2x žlutý motor
* šasi

**Nástroje:**
* zalamovací nůž 


**Postup:**
1. Odlámat přebytečná plastová kolečka. 
    
1. Dočistit zalamovacím nožem.
    
1. Provést podobné očištění od přebytčného plastu i u šasi. 
    
    

1. Protlačit libovolný M3 šroub skrze díry v šasi pro jejich očištění. 
    
1. vytlačený přebytek plastu.
    
1. Nasadit držák na motor. Mezera v držáku směřuje na opačnou stranu než výstupek motoru.
    
1. Posunout držák do pozice.
    
1. Jemně nasunout do pozice v šasi. Přívodní kabely pozicovat tak, aby se při vkládání nikde neskříply.
    
1. Zarovnat na pozici. Zkontrolovat volný pohyb kabelů.
    
1. Výsledný vzhled.
    

## <a name = bocnice2>Sestavení bočnic</a>
**Potřebné díly:**
* osazené šasi motory
* 2x bočnice z překližky
* 4x šroub M3x10 se zápustnou hlavou
* 2x šroub M3x16 se zápustnou hlavou
* 6x matka M3

**Nástroje:**
* šroubovák


**Postup:**
1. Přiložit bočnici z překližky.
    
1. Vložit šroub M3x10 s plochou hlavou a zašroubovat matkou. Matka by měla sama držet v připraveném výřezu. Pokud nedrží, přidržet kleštěmi.
    
1. Obdobně přichytit šroub M3x10 do spodní díry.
    
1. Prošroubovat šroub M3x16 s plochou hlavou zadním uchycením.
    
1. Zachytit při prošroubovávání matku prstem.
    
1. Zopakovat postup pro druhou bočnici.    
1. Výsledný vzhled. Šrouby nesmí výrazně vyčuhovat z plochy bočnice.
    

## <a name = kola>Nasazení kol</a>
**Potřebné díly:**
* osazené šasi
* 2x kolo
* 2x vrut 2,2x10 mm

**Nástroje:**
* šroubovák


**Postup:**
1. Nasadit kolo na osu a přitlačit k bočnici z překližky.
    
1. Zaošroubovat vrut.
    
1. Opakovat postup pro druhé kolo.
    

## <a name = sasi1>Kompletace šasi #1</a>
**Potřebné díly:**
* Osazené šasi motory a koly
* 1x paluba z překližky
* 1x kryt kufru
* 4x šroub M3x10
* 2x šroub M3x8
* 6x matka

**Nástroje:**
* šroubovák
* maticový klíč


**Postup:**
1. Vložit palubu. Zespodu vložit 4x matku do připraveného otvoru.
    
1. 4x zašroubovat šroub.
    
1. Nasunout kryt kufru.
    
1. Prošroubovat 2x šroub a dotáhnout matky.
    
1. Výsledný vzhled.
    

## <a name = bocnice3>Příprava bočnic #2</a>
**Potřebné díly:**
* bočnice z plexiskla


**Postup:**
1. Slepit z obou stran bočnice fólii.
    
1. Opakovat postup pro druhou bočnici.
1. Bočnice je po odstranění folií *zcela průhledná.*

## <a name = sasi2>Kompletace šasi #2</a>
**Potřebné díly:**
* šasi
* 6x malé kolo
* 6x osa kola z 3D tiskárny
* 2x podložka šroubu z 3D tiskárny
* 6x šroub M3x40
* 2x šroub M3x12
* 8x matka
* 2x ložisko kola z 3D tiskárny

**Nástroje:**
* šroubovák
* maticový klíč


**Postup:**
1. Vložit osu kola do kola. Rozevření osy kola je na straně kola, kde jsou matky.
    
1. *Nastavitelné vypínací kolo má navíc podložku šroubu z 3D tiskárny.* Provléct šroub skrz podložku, bočnici z plexiskla osou kola. Hlavy šroubů jsou umístěny směrem k plexisklu.
    
1. Obdobný postup, kromě podložky pod sřoub, zopakovat pro další 2 kola.
    
1. Vložit matku do ložiska z 3D tiskárny. Přitlačit kleštěmi, pokud je potřeba.
    
1. Připravit ložisko. Nožem uvolnit jednotlivé "kuličky" od stěn ložiska i mezi sebou.

1. Prošroubovat ložisko šroubem a přitáhnout k bočnici z překližky.
    
1. Přiložit bočnici k šasi a protáhnout do šasi šrouby od kol.
    
1. Vložit matky do připravených děr. Srovnat 3D tištěnou a dřevěnou bočnici a dotáhnout šrouby.
    
1. Vystřeďovací šroub nechat volně pohyblivý. Vyzkoušet, jestli je možné šroubem pohybovat.
    
1. Obdobný postup zopakovat pro druhou bočnici. Výsledný vzhled.
    

## <a name = serva>Držák servo motoru</a>
**Potřebné díly:**
* držák motorů s jmenovkou z 3D tiskárny
* 2x balení servo motoru 
* 2x šroub M3x12 se zapuštěnou hlavou
* ozubené kolo z 3D tiskárny

**Nástroje:**
* šroubovák



**Postup:**
1. Vložit servo motor do držáku dle nákresu.
    
1. Vytáhnout kabel dle fotografie.
    
1. Na druhý motor natlačit ozubené kolo z 3D tiskárny.
    
1. Prošroubovat šroub dodaný v balení (ten větší, v balení by takové měly být dva) s motorem ozubeným kolem. Vložit obě serva do držáku motorů.
    
1. Oba dráty protáhnout naznačeným způsobem.
    
1. Přišroubovat držák motorů k šasi. Jmenovka je natočená dopředu a čitelná zepředu.
    

## <a name = pohyb>Sestavení senzoru pohybu</a>
**Potřebné díly:**
* 6x díl z 3D tiskárny
* 4x matka
* 4x šroub M3x40

**Nástroje:**
* reflexní páska
* zalamovací nůž
* nůžky
* šroubovák
* maticový klíč


**Postup:**
1. Odlepit kus pásky a zastřihnout.
    
1. Zalepit plochý díl z 3D tiskárny tešně pod dírami.
    
1. Ořezat přebytečnou pásku zalamovacím nožem. Ořezání porvádět na podložce, ne na stole!
    
1. Díly na enkodér nejsou shodné. V jednom díle je výřez, ten se dá vedle plochého dílu (v něm je také výřez).
        
1. Poskládat sendvič dle obrázku. Protáhnout šroub skrz. 
    
1. Umístit do pozice na obrázku. Protáhnout šroub druhou volnou dírou.
    
1. Přitáhnout matky.
    
1. Opakovat postup na druhé straně. Výsledný vzhled.
    

## <a name = radlice>Sestavení radlice</a>
**Potřebné díly:**
* 2x rameno radlice z 3D tiskárny (ozubené a neozubené)
* 2x šroub M3x14 s kulatou hlavou
* 2x podložky z 3D tiskárny
* 4x vrut 2,5x16
* radlice z překližky

**Nástroje:**
* šroubovák
* maticový klíč



**Postup:**
1. Prošroubovat ozubené rameno radlice vrutem. Rameno musí přesně navazovat na díl překližky. Ramena nejsou zaměnitelná, ozubené rameno musí být umístěno podle obrázku.
    
1. Podobně s druhým ramenem. 
    
1. Navléct podložku na šroub.
    
1. Uchytit rameno do bočnice. Utáhnout.
    
1. Obdobně na druhé straně.
    

## <a name = pasy1>Polepení pásů</a>

**Potřebné díly:**
* 4x vytištěný kus pásu
* 2 m těsnění do oken
 
**Nástroje:**
* štípací kleště / nůžky
* 3D tištěné měřidlo



**Postup:**

1. Nastříhejte z pryžové pásky nálepku na každý článek pásu. Bude potřeba 72 kusů těsnění. Použijte 3D tištěné měřítko pro odměření velikosti článků. 

    
1. Každý článek pásů polepte. Na těsnění je pod ochrannou fólií samolepící vrstva. Pokud se vrstva lepidla odlepuje z těsnění, před odlepováním zmáčknout kus těsnění tak, aby vrstva lepidla lépe přilnula k těsnění.

    

## <a name = pasy2>Slepení pásů</a>

**Potřebné díly:**
* 4x 3D tištěné pásy
* kus filamentu
 
**Nástroje:**
* lepidlo na plasty
* nůžky
* kleště
* pravítko

**Postup:**

1. Nastříhejte z filamentu 4 kusy po 0,9 cm.
    
1. Pomocí kleští vsuňte kus filamentu na spojnici mezi pásy.
     
1. Zalepte kus filamentu z obou stran. **Pozor:** Použijte malé množství lepidla, aby se nedostalo do kloubů pásu.
    
1. Lepidlo nechte zaschnout min. 20 minut. Po tuto dobu s pásy výrazně nehýbejte, nesnažte se je nasadit na robota!

## <a name = pasy3>Nasazení pásů</a>

**Potřebné díly:**
* 2x zkompletované pásy
* šasi

**Nástroje:**
* šroubovák

**Postup:**

1. Zajistěte, aby napínací šroub byl v pozici pro nejjednodušší převlečení šroubu.
1. Postupně nasaďte pás. Nejprve nasaďte na velké kolo a pokračujte dopředu. 
   )
1. Vypněte pás a dotáhněte pohyblivé kolo. 
    

## <a name = elektronika>Elektronika</a>

[*Pájení je v samostatném návodu.*](TrackJet_electronics_cz.md)

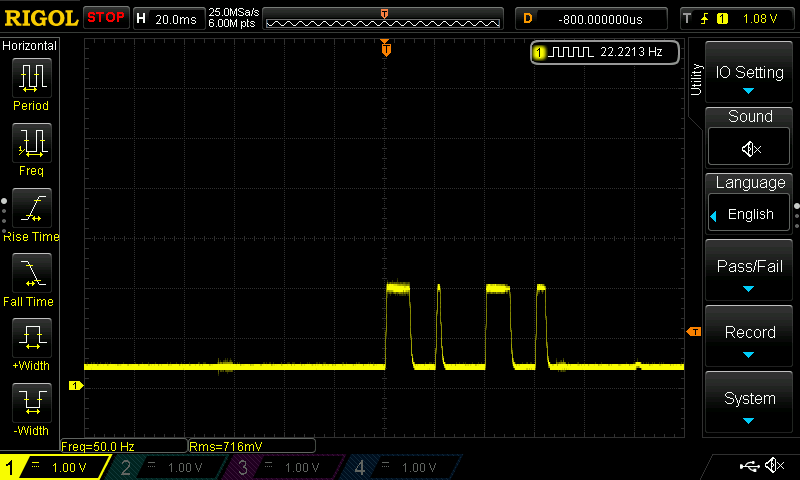
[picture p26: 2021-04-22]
Hardware/Sallen Key filter analysis for current sensing/Sallen Key -3dB@500Hz motor changing position.png

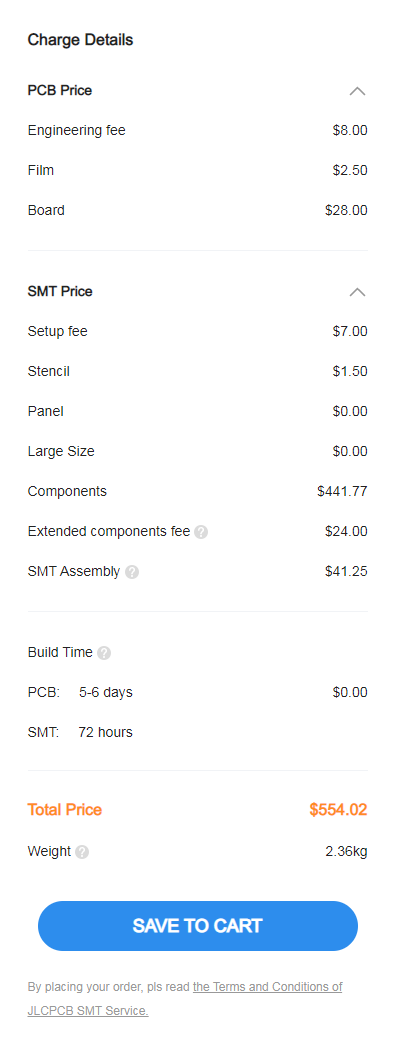
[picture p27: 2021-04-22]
Hardware/Price for 50 PCBS.PNG

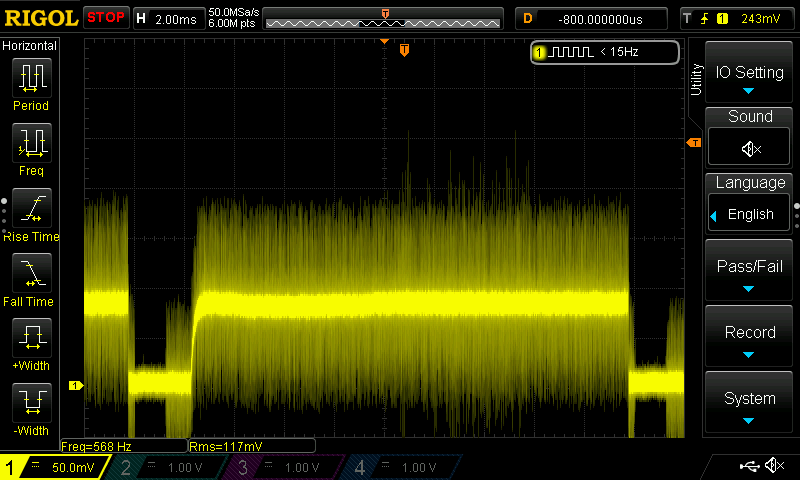
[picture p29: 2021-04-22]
Hardware/Sallen Key filter analysis for current sensing/Pre-filter detail.png

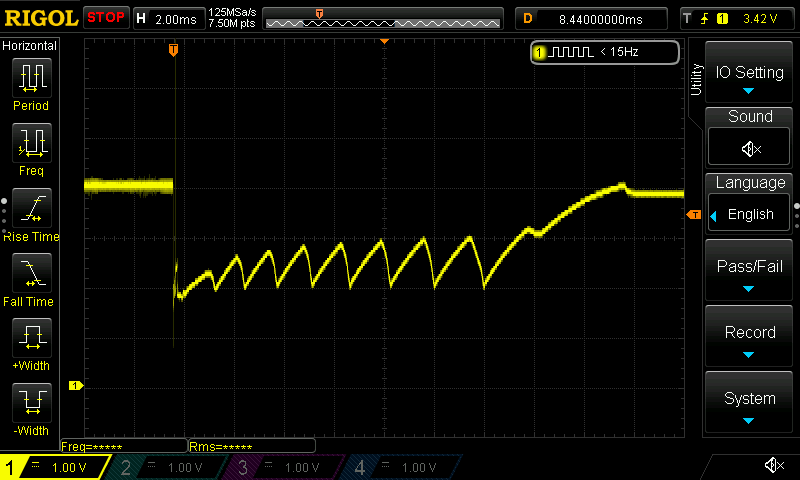
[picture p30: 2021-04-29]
Hardware/TP4056 overheating.png

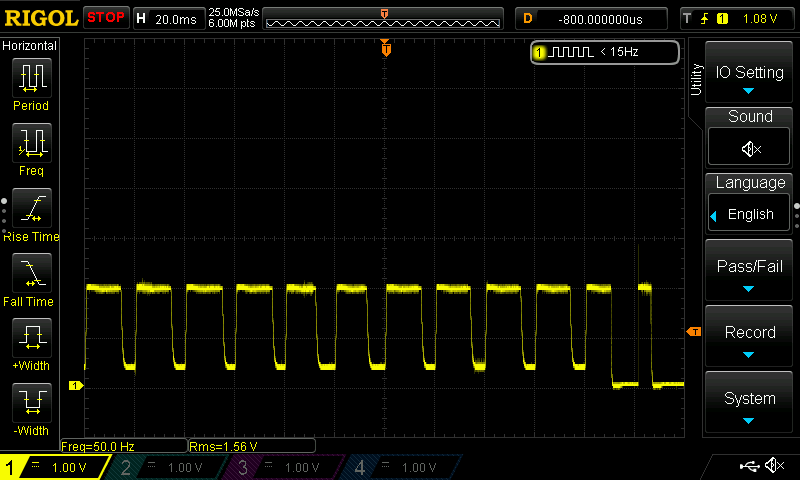
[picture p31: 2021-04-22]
Hardware/Sallen Key filter analysis for current sensing/Sallen Key -3dB@500Hz motor holding.png

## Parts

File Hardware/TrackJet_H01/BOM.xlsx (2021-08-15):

Comment | Designator | Footprint | LCSC
22p | C12,C13 | Capacitor_SMD:C_0603_1608Metric | C1653
1u | C22,C39 | Capacitor_SMD:C_0603_1608Metric | C15849
2u2 | C23 | Capacitor_SMD:C_0603_1608Metric | C23630
10n | C25 | Capacitor_SMD:C_0603_1608Metric | C57112
100n | C1,C2,C3,C4,C6,C7,C9,C11,C14,C15,C16,C17,C18,C19,C20,C21,C40,C42,C44,C46,C47,C48,C50,C53,C55,C56,C59,C60,C61,C68,C71 | Capacitor_SMD:C_0603_1608Metric | C14663
1n | C41 | Capacitor_SMD:C_0603_1608Metric | C1588
10u | C5,C10,C24,C43 | Capacitor_SMD:C_0805_2012Metric | C15850
220n | C64,C65,C69,C70,C72,C73 | Capacitor_SMD:C_0603_1608Metric | C21120
2n2 | C8 | Capacitor_SMD:C_0603_1608Metric | C1604
SS34 | D12 | Diode_SMD:D_SMA | C8678
B5819W | D6,D7,D8,D9,D10,D11,D13,D15 | Diode_SMD:D_SOD-123 | C8598
Fuse 15A | F1 | Fuse:Fuse_1206_3216Metric | C182976
TP4056 | IC1 | Package_SO:SOIC-8-1EP_3.9x4.9mm_P1.27mm_EP2.514x3.2mm_ThermalVias | C382139
TYPE-C-31-M-12 | J5 | Connector_USB:USB_C_Receptacle_HRO_TYPE-C-31-M-12 | C165948
2u2 | L1 | Inductor_SMD:L_Wuerth_HCI-1040 | C149550
22uH | L2 | Inductor_SMD:L_Wuerth_HCI-1040 | C182173
2N7002 | Q1 | Package_TO_SOT_SMD:SOT-23 | C8545
S8050 | Q2,Q3 | Package_TO_SOT_SMD:SOT-23 | C2146
AO3400A | Q6,Q7,Q8,Q9 | Package_TO_SOT_SMD:SOT-23 | C20917
12K | R9,R10 | Resistor_SMD:R_0603_1608Metric | C22790
5K1 | R5,R6,R11,R12 | Resistor_SMD:R_0603_1608Metric | C23186
24K | R15 | Resistor_SMD:R_0603_1608Metric | C23352
150K | R16 | Resistor_SMD:R_0603_1608Metric | C22807
200K | R17 | Resistor_SMD:R_0603_1608Metric | C25811
240K | R18 | Resistor_SMD:R_0603_1608Metric | C4197
30K | R19,R28 | Resistor_SMD:R_0603_1608Metric | C22984
2K2 | R1,R2 | Resistor_SMD:R_0603_1608Metric | C4190
1K | R20,R21,R26,R30,R32,R34,R36,R38,R40 | Resistor_SMD:R_0603_1608Metric | C21190
1M | R22,R46,R52,R61 | Resistor_SMD:R_0603_1608Metric | C22935
3M | R23 | Resistor_SMD:R_0603_1608Metric | C23156
1K2 | R25 | Resistor_SMD:R_0603_1608Metric | C22765
220K | R27 | Resistor_SMD:R_0603_1608Metric | C22961
100R | R13,R14,R29,R31,R33,R35,R37,R39,R41,R65,R66,R67,R68,R69 | Resistor_SMD:R_0805_2012Metric | C17408
10K | R3,R4,R24,R55,R56,R58,R59 | Resistor_SMD:R_0603_1608Metric | C25804
220R | R42,R43 | Resistor_SMD:R_0603_1608Metric | C22962
0R1 | R47,R53,R62 | Resistor_SMD:R_1206_3216Metric | C25334
47K | R48,R54,R63 | Resistor_SMD:R_0603_1608Metric | C25819
1K5 | R49,R57,R64 | Resistor_SMD:R_0603_1608Metric | C22843
22K | R45,R51,R60,R70,R71,R72,R73,R74,R75 | Resistor_SMD:R_0603_1608Metric | C31850
470R | R7,R8 | Resistor_SMD:R_0603_1608Metric | C23179
ESP32-WROOM-32D | U1 | RF_Module:ESP32-WROOM-32 | C473012
74HC595 | U13,U14,U20,U21 | Package_SO:SOIC-16_3.9x9.9mm_P1.27mm | C5947
CD4051B | U15 | Package_SO:SOIC-16_3.9x9.9mm_P1.27mm | C21379
LM358 | U17,U19 | Package_SO:SOIC-8_3.9x4.9mm_P1.27mm | C7950
MPU-6050 | U2 | Sensor_Motion:InvenSense_QFN-24_4x4mm_P0.5mm | C24112
CH340G | U3 | Package_SO:SOIC-16_3.9x9.9mm_P1.27mm | C14267
AMS1117-3.3 | U4 | Package_TO_SOT_SMD:SOT-223-3_TabPin2 | C6186
TPS61088RHLR | U5 | Sergej_Library:IC_TPS61088RHLR | C87357
MT3608 | U6 | Package_TO_SOT_SMD:SOT-23-6 | C84817
DRV8833 | U22 | Package_SO:HTSSOP-16-1EP_4.4x5mm_P0.65mm_EP3.4x5mm_Mask2.46x2.31mm_ThermalVias | C50506

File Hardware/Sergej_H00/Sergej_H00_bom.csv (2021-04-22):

Comment | Designator | Footprint | LCSC
18650 | BT1 | Sergej_Library:BatteryHolder_MPD_BH-18650-PC2_NoHoles
Buzzer | BZ1 | Buzzer_Beeper:Buzzer_12x9.5RM7.6
22p | C12,C13 | Capacitor_SMD:C_0603_1608Metric | C84711
1u | C39 | Capacitor_SMD:C_0603_1608Metric | C15849
100n | C1,C2,C3,C4,C6,C7,C9,C11,C14,C15,C16,C17,C18,C19,C20,C21,C40,C42,C44,C46,C47,C48,C50,C53,C55,C56,C58,C59,C60,C61,C68,C71 | Capacitor_SMD:C_0603_1608Metric | C14663
1n | C41 | Capacitor_SMD:C_0603_1608Metric | C1588
100u | C45,C51,C54 | Capacitor_THT:CP_Radial_D5.0mm_P2.00mm | C43803
1000u 16V | C49,C52,C57 | Capacitor_THT:CP_Radial_D8.0mm_P3.50mm | C43348
10u | C5,C10,C43,C63,C67 | Capacitor_SMD:C_0805_2012Metric | C15850
2n2 | C8,C64,C65,C69,C70,C72,C73 | Capacitor_SMD:C_0603_1608Metric | C1604
LED | D1,D2 | LED_THT:LED_D3.0mm
SS34 | D12 | Diode_SMD:D_SMA | C8678
LED_GREEN | D3 | LED_THT:LED_D3.0mm
LED_RED | D4 | LED_THT:LED_D3.0mm
KYX-1088AS | D5 | Sergej_Library:KYX-1088AS
B5819W | D6,D7,D8,D9,D10,D11 | Diode_SMD:D_SOD-123 | C8598
Fuse 15A | F1 | Fuse:Fuse_1206_3216Metric | C182976
MountingHole | H1,H2,H3,H4 | MountingHole:MountingHole_3.2mm_M3
MountingHole | H5,H6 | Sergej_Library:ZIP_Tie_Slot_Hole
TP4056 | IC1 | Package_SO:SOIC-8-1EP_3.9x4.9mm_P1.27mm_EP2.514x3.2mm_ThermalVias | C16581
Conn_01x06_Female | J1,J2 | Connector_JST:JST_XH_B6B-XH-A_1x06_P2.50mm_Vertical
Conn_01x03_Male | J8,J12,J15 | Connector_PinHeader_2.54mm:PinHeader_1x03_P2.54mm_Vertical
Conn_01x02_Male | J16 | Connector_PinHeader_2.54mm:PinHeader_1x02_P2.54mm_Vertical
Conn_01x05_Male | J3,J4 | Connector_PinHeader_2.54mm:PinHeader_1x05_P2.54mm_Vertical
TYPE-C-31-M-12 | J5 | Connector_USB:USB_C_Receptacle_HRO_TYPE-C-31-M-12 | C165948
Conn_01x01_Male | J6 | Connector_PinHeader_2.54mm:PinHeader_1x01_P2.54mm_Vertical
Conn_01x02 | J7,J9,J10,J11,J13,J14 | Connector_JST:JST_XH_B2B-XH-A_1x02_P2.50mm_Vertical
2u2 | L1 | Inductor_SMD:L_Wuerth_HCI-1040 | C149550
22uH | L2 | Inductor_SMD:L_Wuerth_HCI-1040 | C182173
2N7002 | Q1 | Package_TO_SOT_SMD:SOT-23 | C8545
S8050 | Q2,Q3,Q5 | Package_TO_SOT_SMD:SOT-23 | C2146
AO3400A | Q6,Q7,Q8,Q9 | Package_TO_SOT_SMD:SOT-23 | C20917
12K | R9,R10 | Resistor_SMD:R_0603_1608Metric | C22790
5K1 | R5,R6,R11,R12 | Resistor_SMD:R_0603_1608Metric | C23186
24K | R15 | Resistor_SMD:R_0603_1608Metric | C23352
150K | R16 | Resistor_SMD:R_0603_1608Metric | C22807
270K | R17 | Resistor_SMD:R_0603_1608Metric | C22965
240K | R18 | Resistor_SMD:R_0603_1608Metric | C4197
30K | R19,R28 | Resistor_SMD:R_0603_1608Metric | C22984
2K2 | R1,R2 | Resistor_SMD:R_0603_1608Metric | C4190
1K | R20,R21 | Resistor_SMD:R_0603_1608Metric | C21190
1M | R22,R46,R52,R61 | Resistor_SMD:R_0603_1608Metric | C22935
3M | R23 | Resistor_SMD:R_0603_1608Metric | C23156
51K | R24 | Resistor_SMD:R_0603_1608Metric | C23196
1K2 | R25 | Resistor_SMD:R_0603_1608Metric | C22765
10M | R26 | Resistor_SMD:R_0603_1608Metric | C7250
220K | R27 | Resistor_SMD:R_0603_1608Metric | C22961
100R | R13,R14,R29,R31,R33,R35,R37,R39,R41,R65,R66,R67,R68,R69 | Resistor_SMD:R_0805_2012Metric | C17408
10K | R3,R4,R30,R32,R34,R36,R38,R40,R55,R56,R58,R59 | Resistor_SMD:R_0603_1608Metric | C25804
220R | R42,R43 | Resistor_SMD:R_0603_1608Metric | C22962
56K | R44,R50 | Resistor_SMD:R_0603_1608Metric | C23206
0R1 | R47,R53,R62 | Resistor_SMD:R_1206_3216Metric | C25334
47K | R48,R54,R63 | Resistor_SMD:R_0603_1608Metric | C25819
1K5 | R49,R57,R64 | Resistor_SMD:R_0603_1608Metric | C22843
22K | R45,R51,R60,R70,R71,R72,R73,R74,R75 | Resistor_SMD:R_0603_1608Metric | C31850
470R | R7,R8 | Resistor_SMD:R_0603_1608Metric | C23179
R_POT | RV1 | Potentiometer_THT:Potentiometer_Alps_RK09K_Single_Vertical
Rotary_Encoder_Switch | SW1 | Rotary_Encoder:RotaryEncoder_Alps_EC11E-Switch_Vertical_H20mm
SW_DPST | SW2 | Button_Switch_THT:SW_TH_Tactile_Omron_B3F-10xx
MT-102 | SW3 | Sergej_Library:TE_A101SYCQ04
ESP32-WROOM-32D | U1 | RF_Module:ESP32-WROOM-32 | C473012
TCRT5000 | U9,U10,U11,U12 | Sergej_Library:TCRT5000_SMD
74HC595 | U13,U14,U20,U21 | Package_SO:SOIC-16_3.9x9.9mm_P1.27mm | C5947
CD4051B | U15 | Package_SO:SOIC-16_3.9x9.9mm_P1.27mm | C21379
DRV8871DDA | U16,U18 | Package_SO:Texas_HTSOP-8-1EP_3.9x4.9mm_P1.27mm_EP2.95x4.9mm_Mask2.4x3.1mm_ThermalVias | C75864
LM358 | U17,U19 | Package_SO:SOIC-8_3.9x4.9mm_P1.27mm | C7950
MPU-6050 | U2 | Sensor_Motion:InvenSense_QFN-24_4x4mm_P0.5mm | C24112
CH340G | U3 | Package_SO:SOIC-16_3.9x9.9mm_P1.27mm | C14267
AMS1117-3.3 | U4 | Package_TO_SOT_SMD:SOT-223-3_TabPin2 | C6186
TPS61088RHLR | U5 | Sergej_Library:IC_TPS61088RHLR | C87357
MT3608 | U6 | Package_TO_SOT_SMD:SOT-23-6 | C84817
TCRT5000 | U7,U8 | Sergej_Library:TCRT5000
12MHz | Y1 | Crystal:Crystal_HC49-4H_Vertical

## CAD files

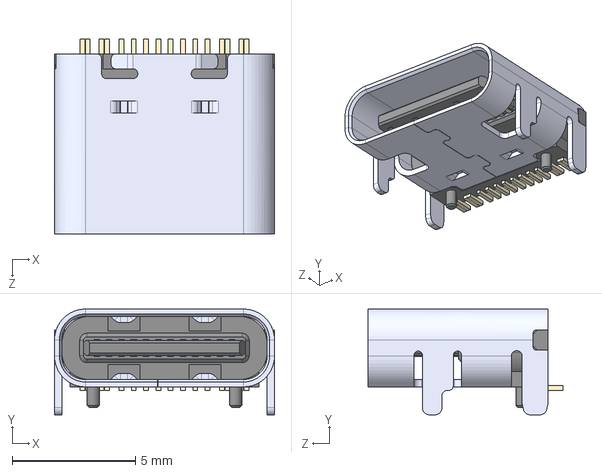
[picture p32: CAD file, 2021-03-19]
Hardware/TrackJet_H01/Sergej_Libraries/TYPE-C-31-M-12--3DModel-STEP-56544.STEP
8.94 x 4.30 x 7.90 mm

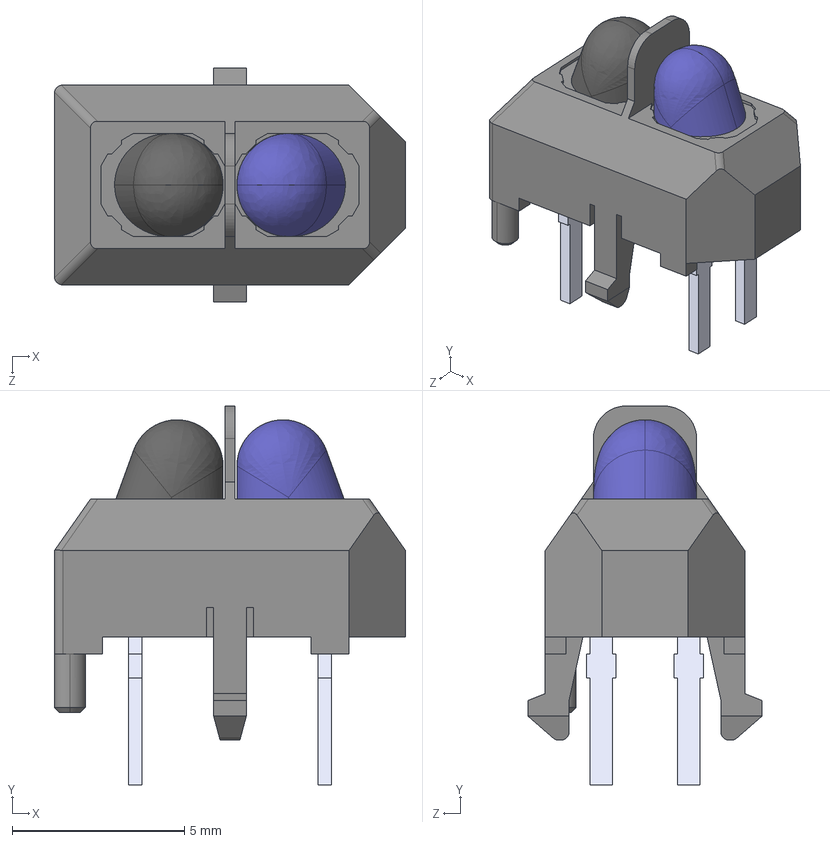
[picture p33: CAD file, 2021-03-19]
Hardware/TrackJet_H01/Sergej_Libraries/TCRT5000.step
10.2 x 11.0 x 6.80 mm

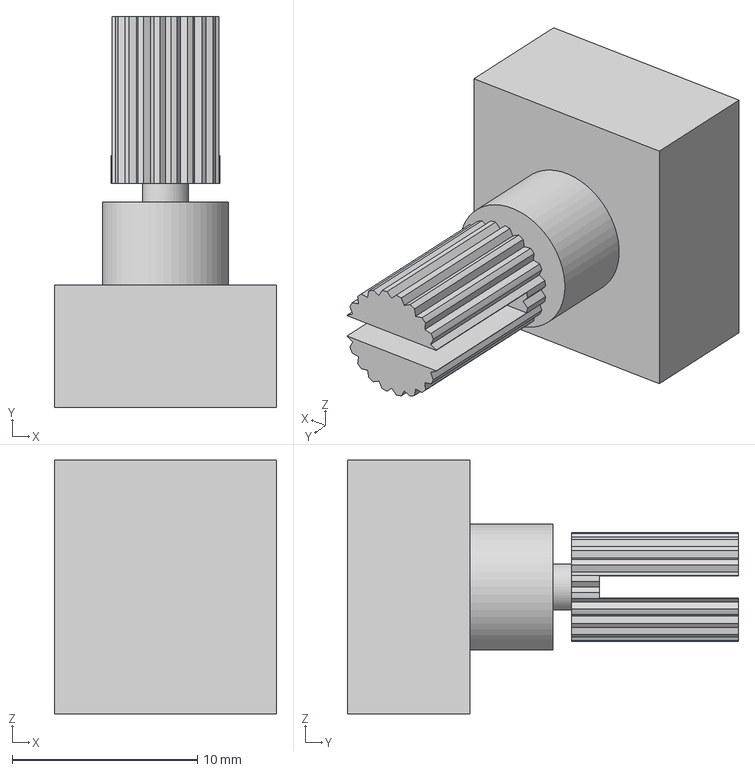
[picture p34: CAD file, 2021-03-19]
Hardware/TrackJet_H01/Sergej_Libraries/QuadEnc_plum_15mm.step
12.0 x 21.1 x 13.7 mm

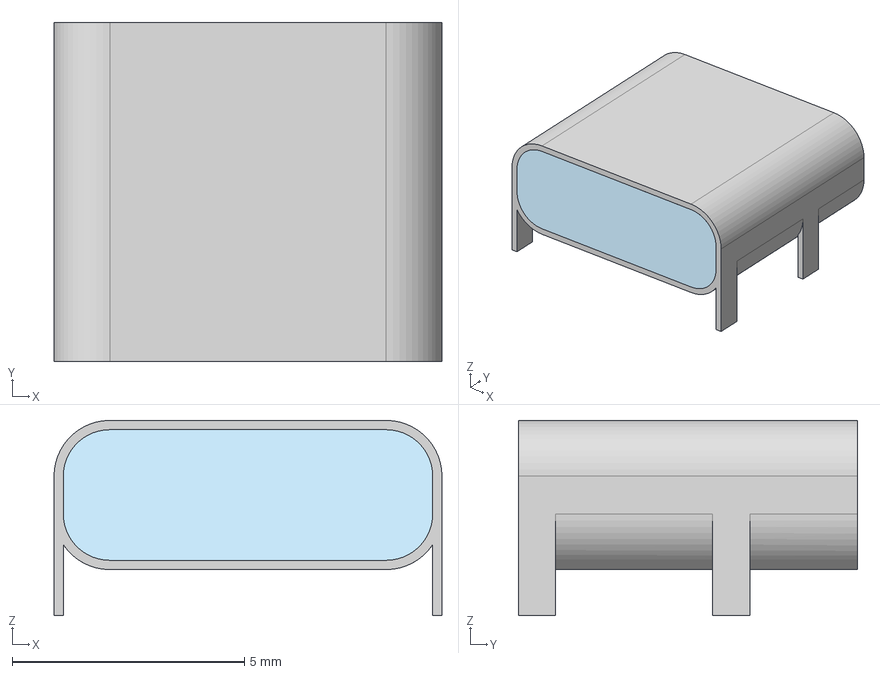
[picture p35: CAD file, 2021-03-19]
Hardware/TrackJet_H01/Sergej_Libraries/USB-C_THT.step
8.35 x 7.30 x 4.20 mm

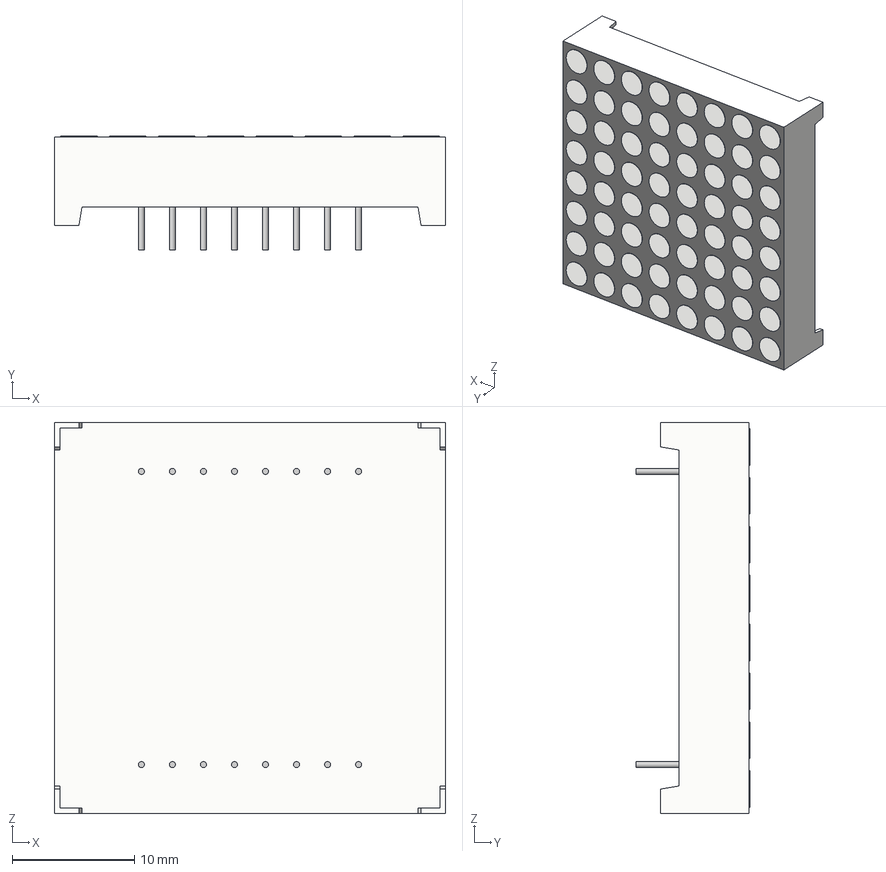
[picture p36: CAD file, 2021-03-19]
Hardware/TrackJet_H01/Sergej_Libraries/LED Matrix 3mm 8x8.step
32.0 x 9.30 x 32.0 mm

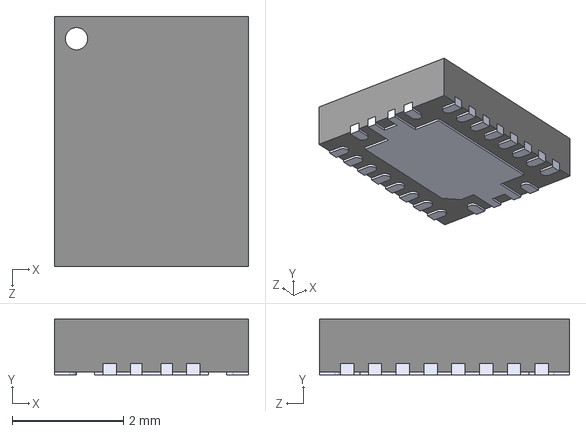
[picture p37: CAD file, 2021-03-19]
Hardware/TrackJet_H01/Sergej_Libraries/TPS61088RHLR.step
3.50 x 1.00 x 4.50 mm

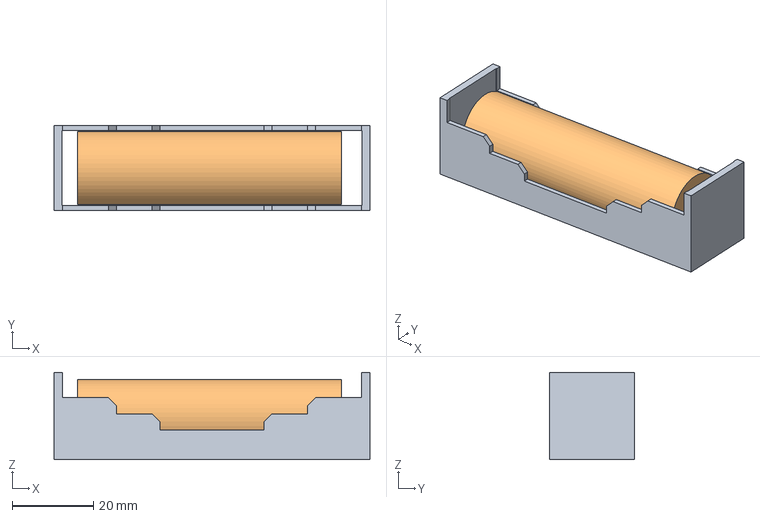
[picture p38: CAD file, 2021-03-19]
Hardware/TrackJet_H01/Sergej_Libraries/18650_case_batt.step
77.8 x 21.0 x 21.5 mm

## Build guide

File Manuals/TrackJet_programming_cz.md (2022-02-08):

Toto je návod na programování robotického pásového vozidla TrackJet. Začneme instalací vývojového prostředí na váš PC, následně si ukážeme základní pravidla programovacího jazyka C++ a poté začneme využívat funkce robota TrackJet.

V tomto návodu se budeme zabývat programováním mikrokontroléru (mikropočítače) ESP32. K tomu je od výrobce ESP32 připraven framework (sada nástrojů urychlujících vývoj) ESP-IDF v jazyce C. Nadstavbou tohoto frameworku je další framework [arduino-esp32](https://github.com/espressif/arduino-esp32), který přidává další sadu nástrojů a je již napsán v jazyce C++. Arduino-esp32 používáme v našem projektu pro TrackJet. Bylo k němu potřeba přidat množství kódu (knihovna *TrackJet*), který se stará o *základní životní funkce* TrackJet a umožňuje jednodušší používání jeho funkcionalit (z `main.cpp`). V tomto návodě se budeme zabývat jen uživatelským pohledem na používání knihovny *TrackJet*.

___
# Obsah
* [Vývojové prostředí](#IDE)
* [Dálkové ovládání - kontrola robota](#kontrola)
* [Nový projekt](#novyProjekt)
* [První program](#prvniProgram)
* [Komentáře](#komentare)
* [Proměnné](#promenne)
* [Podmínky](#podminky)
* [Cyklus](#cyklus)
* [Funkce](#funkce)
* [LEDky](#ledky)
* [Tlačítko](#tlacitko)
* [Potenciometr](#potenciometr)
* [Sériová linka](#seriovka)
* [Motory](#motory)
* [Enkodér](#enkoder)
* [Serva](#serva)
* [LIDAR](#lidar)
* [Výpis textu na LED panel](#panelLed)
* [Bzučák](#buzzer)
* [Senzor čáry](#cara)
* [WiFi](#wifi)
* [Vzdálený příkazový řádek](#remoteCmd)
* [Měření ujeté vzdálenosti](#odometr)
___
## <a name = IDE>Vývojové prostředí</a>

Pro programování TrackJet je použito vývojové prostředí [Visual Studio Code](https://code.visualstudio.com/download) s rozšířením PlatformIO. Pro instalaci prostředí a rozšíření můžete použít tento [návod](https://docs.platformio.org/en/latest/ide/vscode.html#installation), jehož hlavní část je na obrázku níže:

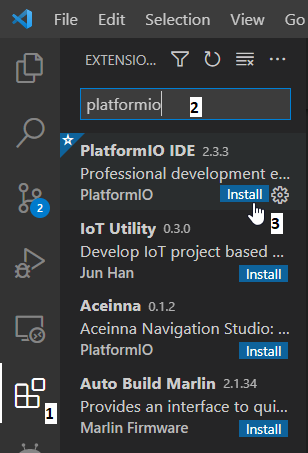
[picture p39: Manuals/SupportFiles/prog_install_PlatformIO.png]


___
## <a name = kontrola>Dálkové ovládání - kontrola robota</a>

V této části nahrajete do TrackJet připravený program pro jeho otestování. Program umožňuje dálkové ovládání TrackJet pomocí tvého chytrého zařízení.

1. Pro naprogramování TrackJet si stáhněte [tento repozitář](https://github.com/vedatori/TrackJet/archive/refs/heads/main.zip). Stáhnutý soubor *TrackJet-main.zip* si rozbalte na disk svého PC na libovolnou lokaci tak, abyste ho našli. 
**Pozor:** PlatformIO nedokáže pracovat s diakritikou v cestě k projektu. Projekt tedy nesmí být součástí složky, která má diakritiku v názvu. Všechny projekty musí být uloženy v cestě bez háčků a čárek!
Pokud vaše uživatelské jméno obsahuje diakritiku, tak nemůžete používat Plochu ani složku Dokumenty, ale musíte vytvořit například *C:/Vedatori/TrackJet-main*.

1. Ve VS Code otevřete nabídku *File*, klikněte na *Open Folder* a zvolte složku *RemoteControl* z dříve rozbalené sbírky příkladů *TrackJet-main*.

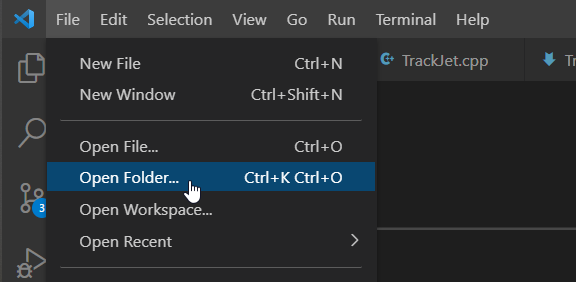
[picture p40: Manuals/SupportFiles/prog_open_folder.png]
    
1. Otevřete soubor *main.cpp* který je v cestě *RemoteControl/src/main.cpp*.

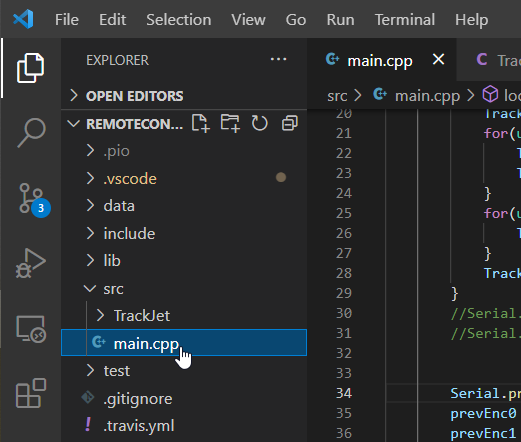
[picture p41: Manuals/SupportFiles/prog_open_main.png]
    
1. V souboru *main.cpp* upravte název robota "<your_name>" tak, aby byl poznatelný, např. jako "MarPta" nebo "MartinP". 
Je možné přidat i heslo pro přihlašování např. takto
"`TrackJet.startWiFiCaptain("<your_name>", "12345678");`".
Heslo musí mít minimálně 8 znaků, jinak nebude použito.

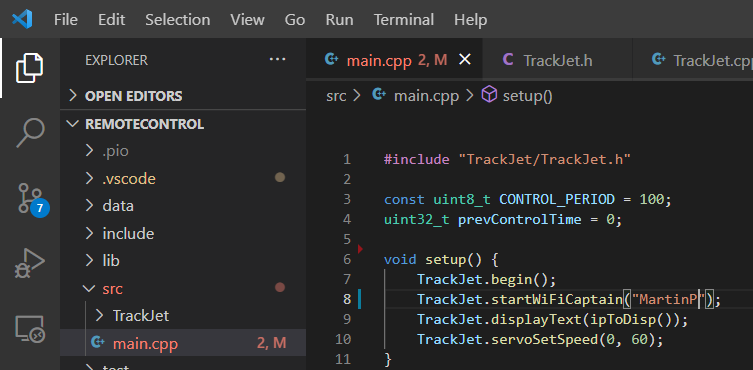
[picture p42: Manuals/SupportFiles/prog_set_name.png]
    
1. Po otevření projektu bude VS Code chvíli pracovat. Pokud ještě pracuje, počkejte, dokud text na dolní liště nezmizí.
   
    
1. Připojte TrackJet pomocí USB-C kabelu k PC.
1. V dolní liště PlatformIO stiskněte šipku a tím nahrejte program do TrackJet.

    
1. Počkejte, až se dokončí nahrávání a zobrazí v dolním terminálu *SUCCESS*.

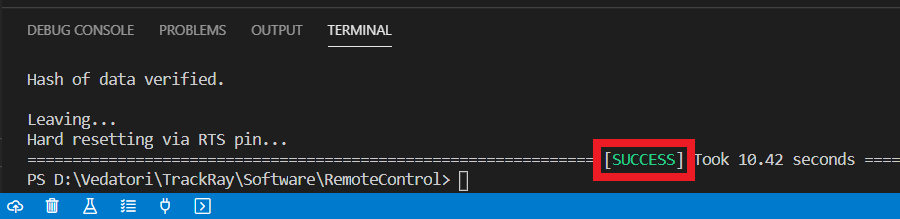
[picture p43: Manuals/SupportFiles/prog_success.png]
    
1. V dolní liště PlatformIO stiskněte tlačítko úplně v pravo a tím spusťe PlatformIO terminál.

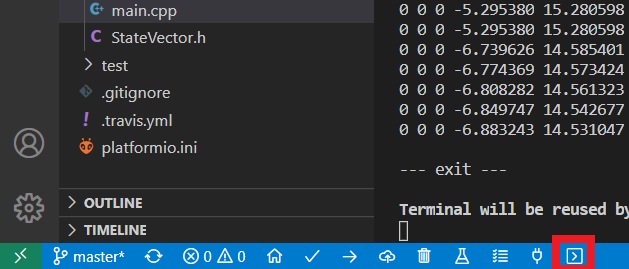
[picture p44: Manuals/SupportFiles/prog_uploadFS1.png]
    
1. Do nově otevřeného termínálu v dolní částí VS Code zadejte příkaz `pio run -t uploadfs` a stiskněte *ENTER*.

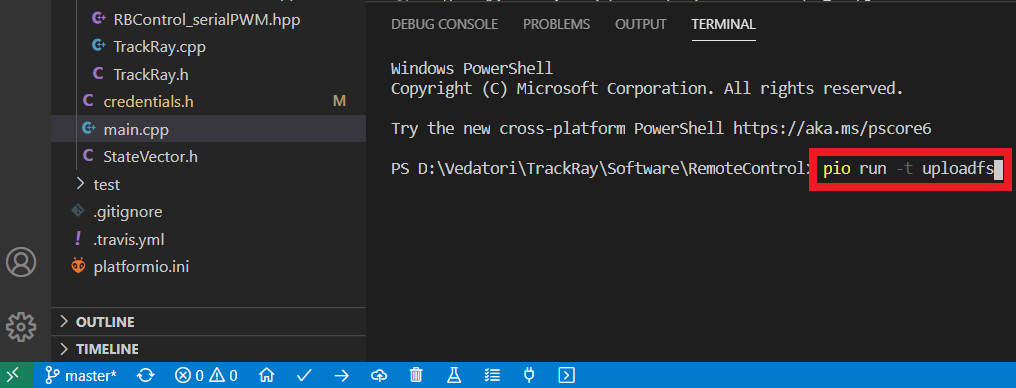
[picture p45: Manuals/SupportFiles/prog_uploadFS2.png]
    
1. Počkejte, až se dokončí nahrávání a zobrazí v dolním terminálu *SUCCESS*.

    
1. Nyní je robot plně naprogramován. Pro ovládání na svém chytrém zařízení vyhledejte WiFi síť s názvem *TrackJet_<your_name>*. Zadejte do webového prohlížeče adresu *192.168.4.1* nebo jakoukoli jinou ve tvaru *www.neco.cz*. Načte se hlavní stránka pro ovládání TrackJet. Joystickem ovládejte pohyb. Na počítači můžete použít i šipky. Do políčka *Command entry* můžete zadávat speciální příkazy.

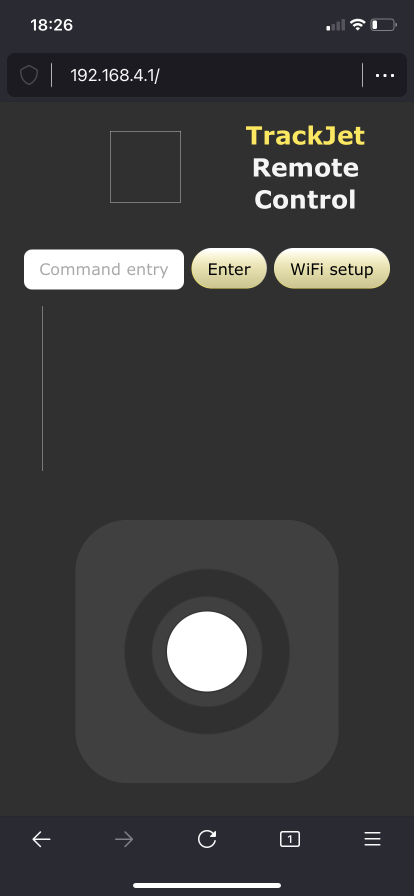
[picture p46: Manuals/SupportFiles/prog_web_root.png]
    
1. Pro přihlášení TrackJet k externí WiFi síti klikněte na tlačítko *WiFi setup*. Na následující stránce zadejte přihlašovací údaje od externí WiFi a potvrďte přihlášení. Poté je potřeba restartovat TrackJet a znovu se k němu připojit.

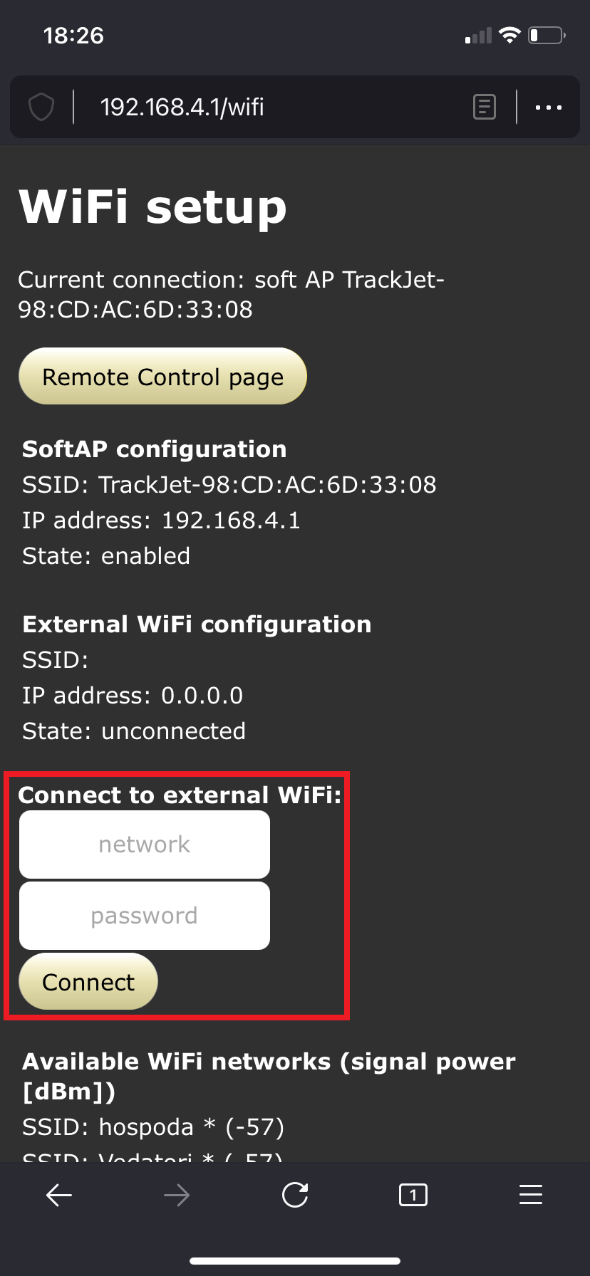
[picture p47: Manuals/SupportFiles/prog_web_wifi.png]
    
1. Pokud přihlášení k externí WiFi proběhne úspěšně, objeví se potvrzení *connected* a přidělená IP adresa. Tato síť bude uložena a vyhledána i po restartu. Připojte se se svým chytrým zařízením také na externí WiFi a zadejte do prohlížeče IP adresu přidělenou TrackJet. V tomto případě *192.168.88.197*. Tato adresa bude po restartu zobrazena i na LED panelu TrackJet. 

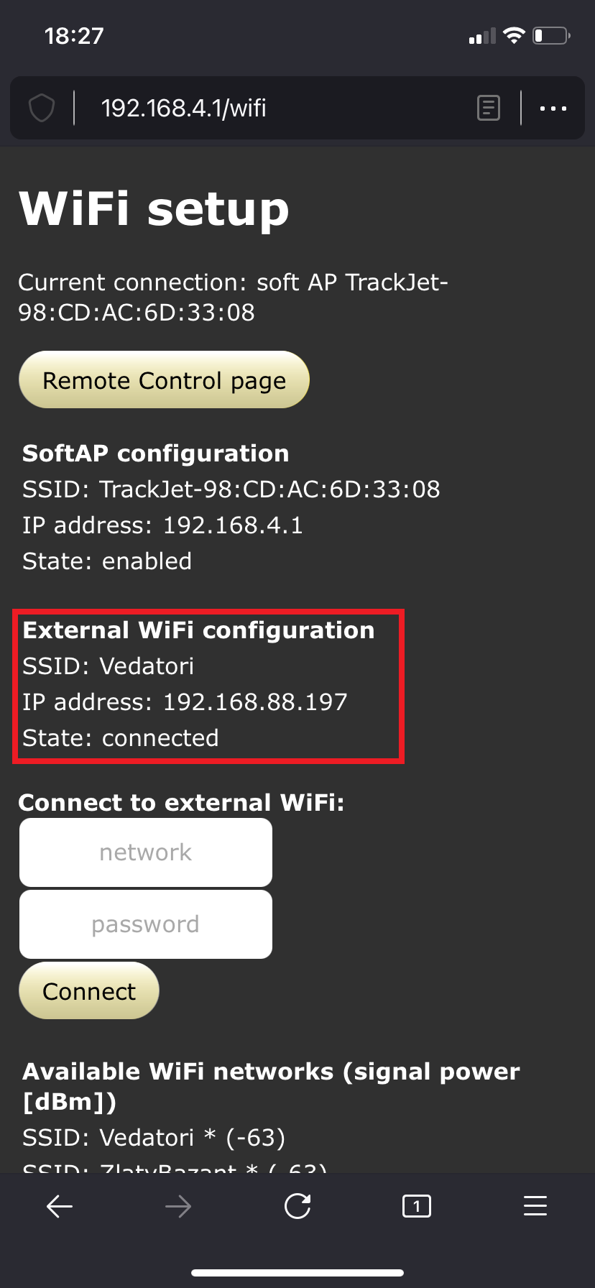
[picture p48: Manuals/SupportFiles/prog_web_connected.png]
    
1. Načte se opět hlavní stránka ovládání TrackJet. Tímto je vypnuta interní WiFi *TrackJet_<your_name>*. Pro její opětovné zapnutí přejděte do nastavení WiFi a klikněte na tlačítko *Enable AP* nebo restartujte TrackJet.

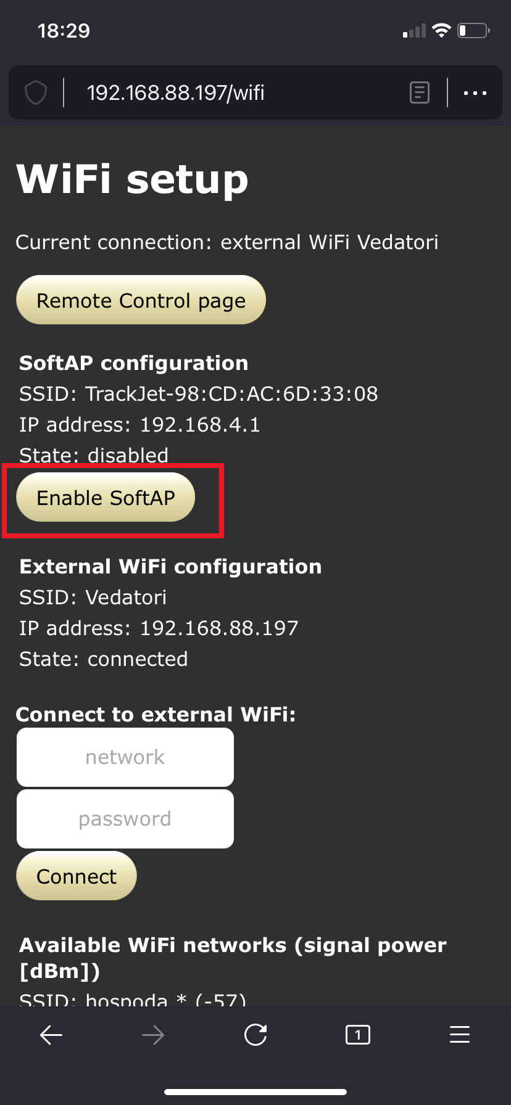
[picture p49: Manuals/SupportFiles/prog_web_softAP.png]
    
1. Pro ovládání TrackJet s připraveným programem můžete používat následující příkazy. Příkazy nejsou citlivé na velikost použitých písmen.
    * `blade <angle>` - Nastaví výšku radlice na daný úhel serva. 0-dole, 180-nahoře
    * `head <angle>` - Nastaví pozici serva LIDARu. 0-vpravo, 180-vlevo
    * `beep` - Zapne buzzer na 0,5 vteřiny na frekvenci 1000Hz
    * `take on me` - Zahraje píseň *Take on me* 
    * `silence` - Zastaví přehrávání písně
___
## <a name = novyProjekt>Nový projekt</a>

Vytvoříme nový projekt a nahrajeme program do TrackJet.

1. Vytvořte si na disku svého PC složku pro vaše budoucí programy, například *C:/TrackJet-moje-programy*.
1. Do této nové složky překopírujte složku *RemoteControl* ze stáhnutého repozitáře *TrackJet-main*. Tato složka bude sloužit jako šablona tvých budoucích programů pro TrackJet. 
1. Překopírovanou složku *RemoteControl* přejmenuj novým názvem, například na *01_prvni_program*.
1. Ve VS Code otevřete složku *01_prvni_program* pomocí *File*->*Open folder*.
1. Ve VS Code otevřete soubor *main.cpp* a nahraď jeho obsah následujícím kódem šablony:
    ```
    #include "TrackJet/TrackJet.h"

    void setup() {
        TrackJet.begin();
    }

    void loop() {
        
    }
    ```
1. Připojte TrackJet pomocí USB-C kabelu k PC.
1. V dolní liště PlatformIO stiskněte šipku (*Upload*) a tím nahrajte program do TrackJet.
    
1. Počkejte až se dokončí nahrávání a zobrazí v dolním terminálu *SUCCESS*. Nyní je nový program nahrán.
    

___
## <a name = prvniProgram>První program</a>
Rozebereme si každý řádek šablony a napíšeme náš první program.

Zde je kód šablony:
```
#include "TrackJet/TrackJet.h"

void setup() {
    TrackJet.begin();
}

void loop() {
    
}
```

1. `#include "TrackJet/TrackJet.h"` - Příkaz *#include* přidává do našeho programu kód z jiných míst. Nyní nám stačí přidání knihovny *TrackJet.h* ze složky TrackJet.
1. `void setup() {}` - Toto je definice funkce. Funkce jsou kusy kódu, které můžeš opakovaně spustit tak, že zavoláš jméno. Kód (tělo) funkce je ohraničen složenými závorkami { a }, a mezi nimi odsazen. Tato funkce se jmenuje *setup* a je spuštěna jedenkrát po zapnutí TrackJet. O to se postará arduino-esp32 framework.
1. `TrackJet.begin();` - Toto je volání funkce z knihovny *TrackJet*, která knihovnu inicializuje a připraví všechny její komponenty pro budoucí použití. Toto je třeba provést pouze jednou po startu robota, proto je příkaz umístěn ve funkci *setup*.
1. `void loop()` - Toto je definice funkce *loop*. Ta je spouštěna stále pořád dokola dokud je TrackJet zapnutý.

### Váš kód
Nyní napíšete svůj první vlastní program pro TrackJet. Na konec funkce *setup* připiště `TrackJet.ledWrite(1, true);`, tedy nad uzavírací závorku }. Tento příkaz zapříčiní, že se LED číslo 1 rozsvítí.

Všimněte si, že při psaní vám VS Code napovídá. Stačí napsat `TrackJet.` a uvidíte nabídku připravených funkcí z knihovny *TrackJet*. Pokud se tak nestane, nabídku vyvoláte stisknutím *Ctrl + Space*.

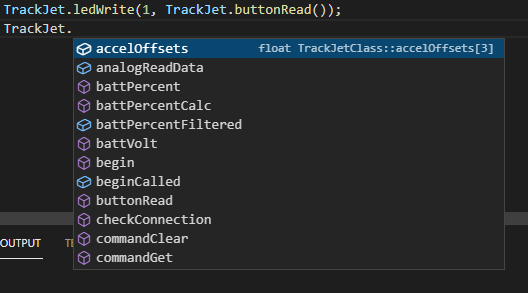
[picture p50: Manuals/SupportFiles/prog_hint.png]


Funkce *ledWrite* slouží k zapínání a vypínání LED světel na TrackJet. Jedná se o volání funkce s parametry v kulatých závorkách ( a ).
1. parametr udává, kterou LED chceme ovládat. V tomto případě budeme ovládat první LED, která se jmenuje *D1*.
1. parametr udává, jestli má LED od nyní svítit (`true`) nebo nesvítit (`false`).

Nahrajte program do TrackJet a počkejte, až se první LED rozsvítí. Gratulujeme, toto byl váš první vlastní program pro TrackJet :-)

___
## <a name = komentare>Komentáře</a>

Do svého kódu je někdy vhodné psát komentáře. Komentáře jsou kusy textu, které jsou viditelné pro programátora, čili vás, ale TracJet si jich nevšímá (ani se do něj nenahrají). Jsou vhodné zejména v místech, kdy ze samotného funkčního kódu není zřejmé, co dělá a k čemu slouží.

V jazyce C++ máme 2 typy komentářů:
1. Jenořádkový komentář je uvozen dvojitým lomítkem `//`. Celý zbytek řádku za dvojitým lomítkem je považován za komentář.
1. Víceřádkový komentář je uvozen lomítkem a hvězdičkou `/*`. Ukončen je hvězdičkou a lomítkem `*/`. Veškerý text mezi je považován za komentář. Začátek a konec mohou být na různých řádcích.

Příklad: Tento program nerozsvítí LEDku.
```
#include "TrackJet/TrackJet.h"

void setup() {
    TrackJet.begin();
    //TrackJet.ledWrite(1, true);
}

void loop() {
    
}
```

___
## <a name = promenne>Proměnné</a>

### Motivace
Při psaní programů brzy dojdete k tomu, že potřebujete, aby si program něco *zapamatoval*. Může se jednat o výsledek matematicé operace, počítadlo kroků, uchování měřené hodnoty a tak dále. K tomuto účelu se v programech používají **proměnné**. Proměnné si můžeme představovat jako šuplíky s textovými popisky na sobě. Do šuplíku můžeme *vložit* nějakou informaci a někdy později ji opět vytáhnout. Popisek šuplíku zde představuje název proměnné.

### Vytvoření proměnné
Proměnnou vytvoříme následujícím příkazem:
```
typ_promenne nazev_promenne = hodnota;
```
`typ_promenne` udává jaký typ informace budeme do proměnné ukládat. Říkáme mu také *datový typ proměnné*. Může to být číslo, text atd.

`nazev_promenne` udává název proměnné, pomocí kterého dokážeme od sebe jednotlivé proměnné odlišit. Proto musí mít každá proměnná svůj jedinečný název. Snaž se pojménovávat proměnné výstižně, tedy např. *rychlost* je mnohem lepší než *prom*. V názvu proměnné můžeš používat znaky anglické abecedy, tj. bez diakritiky, velká a malá písmena, čísla a speciální znaky jako podrtžítko `_`. Podtžítkem můžeme oddělovat slova v názvu jedné proměnné.

`=` je operátor sloužící k přiřazení (vložení) určité hodnoty do proměnné.

`;` čili středník slouží k oddělování příkazů a píšeme ho vždy na konec příkazu. Na české klávesnici se nachází pod klávesou *ESC* vlevo nahoře.

### Základní datové typy proměnných
* `int` označuje proměnnou pro ukládání celých čísel, například `3`.
* `float` označuje proměnnou pro ukládání desetinných čísel, například `3.14`.
* `char` označuje jeden textový znak -> znak se udává v apostrofech, například `'c'` označuje znak *c*.
* `bool` označuje pravdivostní hodnotu -> *true* pro pravdu a *false* pro nepravdu.
* `std::string` označuje řetězec textových znaků -> řetězec se ohraničuje uvozovkami, například `"Ahoj svete"`.

### Operace s proměnnými

Operace *přiřazení* slouží k uložení dané hodnoty do proměnné. Hodnota, která je napravo od rovnítka `=` je uložena do proměnné uvedené nalevo od `=`: 
```
nazev_promenne = hodnota;
```

Číselné proměnné můžeme sčítat (+), odečítat (-), násobit (*) a dělit (/). 

Příklad:
```
#include "TrackJet/TrackJet.h"

void setup() {
    TrackJet.begin();
    int cele_cislo = 0;
    cele_cislo = cele_cislo + 10;   // Zvýšíme hodnotu v proměnné o 10
    cele_cislo += 10;   // Zkrácený zápis stejné operace jako výše
    // Nyní je v proměnné cele_cislo uložena hodnota 20
}

void loop() {
    
}
```

Zde jsou uvedeny příklady vytvoření proměnných zmíněných datových typů a uložení hodnoty do nich.
```
// proměnná pro celá čísla se jménem cele_cislo, ve které je hodnota 0
int cele_cislo = 0; 

// promenna pro desetinne cislo ve které je hodnota 3.14
float desetinne_cislo = 3.14; 

// proměnná znak, do které jsme uložili znak 'a'
char znak = 'a';

// proměnná otevreno, do které jsme uložili hodnotu pravda (true)
bool otevreno = true; 

// proměnná pro textový řetězec s hodnotou "nejaky text"
String text = "nejaky text";
```
___
## <a name = podminky>Podmínky</a>

### Motivace
Při programování brzo zjistíte, že potřebujete, aby se váš program choval různě v různých situacích. Jinými slovy aby prováděl určité úseky kódu pouze za splnění daných podmínek. K tomu se používají *podmínky*. Ty umožňují programu provádět *rozhodnutí*.

### Konstrukce `if`
`if` je základní podmínka. Základem této konstrukce je *podmínka*, která se uvádí za `if` do kulatých závorek. Podmínka může být proměnná nebo logický výraz.
```
if(podminka) {
    ...kód který se provede, pokud je podmínka splněna (true)...
}
```
U `if` konstrukce docházi k vyhodnocení podmínky, tj. zjistí se, zda je podmínka pravdivá (`true`) nebo nepravdivá (`false(`). Pokud je pravdivá, provede se kód, který je za `if` uveden ve složených závorkách `{...kód...}`. V opačném případě program pokračuje až za `if`.

### Konstrukce `else`
Může existovat jen v případě, že před ní byl uvedený `if`. Úkolem `else` je provést kód v něm napsaný jen v případě, že předchozí `if` nebyl splněn.
```
if(podminka) {
    ...kód který se provede, pokud je podmínka splněna (true)...
}
else {
    ...kód který se provede, pokud není podmínka splněna (false)...
}
```

### Konstrukce `else if`
Pokud chceme postihnout více možných příapadů než dva dříve zmíněné (`true` a `false`), použijeme konstrukci `else if`.
```
if(podminka_1) {
    ...kód který se provede, pokud je podmínka 1 splněna (true)...
}
else if(podminka_2) {
    ...kód který se provede, pokud je podmínka 2 splněna (true)...
}
else {
    ...kód který se provede, pokud není podmínka 1 ani 2 splněna (false)...
}
```

Poznámka: V jednotlivých konstrukcích větvení je možné libovolně vnořovat další konstrukce větvení.

### Podmínka
Podmínka dotazovaná při větvení určuje zda se bude daný úsek kódu provádět. K tomu je porovnávána s logickými hodnotami `true` a `false`. Tato hodnota může být uložena v pravdivostní proměnné typu `bool`:
```
bool podminka = true;
if(podminka) {
    ...kód je vykonán, protože podmínka je pravdivá...
}
```

K vytvoření podmínky z číselné hodnoty budeme používat tzv. *relační operátory*:
* `==` označuje porovnávání, takže 1 == 1 označuje, že se 1 rovná 1
* `!=` vykřičník před rovnítkem označuje opak, tudíž tento operátor značí nerovnost, tedy 1 != 2 označuje, že se 1 nerovná 2
* `<` menší než
* `>` větší než
* `<=` menší nebo rovno než
* `>=` větší nebo rovno než
Výsledek výrazu s relačními operátory nabývá hodnotu pravda `true` nebo nepravda `false`.
Příklad relačního operátoru:
```
int cele_cislo = 3;
if(cele_cislo < 5) {
    if (cele_cislo > -5) {
        cele_cislo = 0;
    }
}
// V proměnné cele_cislo je uložena hodnota 0, protože obě podmínky byly splněny
```

### Propojování podmínek
Podmínky je možné propojovat do jedné složitější pomocí logických operátorů. Jsou jimi
* `&&` (logické *A*) říká nám, že musí platit obě podmínky, aby byla podmínka splněna, jinak je nesplněna
* `||` (logické *NEBO*) říká nám, že musí platit alespoň jedna podmínka z nich, aby byla podmínka splněna, jinak je nesplněna
Ukázka: Následující program funguje stejně jako předchozí, používá ovšem využívá logické operátory.
```
int cele_cislo = 3;
if(cele_cislo < 5 && cele_cislo > -5) {
    cele_cislo = 0;
}
// V proměnné cele_cislo je uložena hodnota 0, protože obě podmínky byly splněny
```
___
## <a name = cyklus>Cyklus</a>

### Motivace
Při programování se nám často stane, že potřebujeme některé úkony vykonat vícekrát. Případně vykonat velké množství podobných úkonů. K tomuto budeme používat *cykly*, které nám umožní opakovaně vykonávat úseky kódu.

Pro jedno bliknutí LEDkou poslouží tento program:
```
#include "TrackJet/TrackJet.h"

void setup() {
    TrackJet.begin();
    TrackJet.ledWrite(1, true);
    delay(500);
    TrackJet.ledWrite(1, false);
    delay(500);
}

void loop() {
    
}
```
V tomto programu používáme příkaz *delay()* pro čekání na místu v kódu o určitý čas. Tento čas čekání je určen v milisekundách (1000 ms = 1s).

Pro 3 bliknutí LEDkou poslouží tento program, ve kterém jsme pouze zopakovali příkazy z minulého:
```
#include "TrackJet/TrackJet.h"

void setup() {
    trrBegin();
    TrackJet.ledWrite(1, true);
    delay(500);
    TrackJet.ledWrite(1, false);
    delay(500);

    TrackJet.ledWrite(1, true);
    delay(500);
    TrackJet.ledWrite(1, false);
    delay(500);

    TrackJet.ledWrite(1, true);
    delay(500);
    TrackJet.ledWrite(1, false);
    delay(500);
}

void loop() {
    
}
```

Ale co kdybychom chtěli bliknout 1000 krát? Kód by nás přerostl. Cykly nám pomohou tento problém vyřešit. 

### Cyklus `while`
Cyklus `while` použijeme v případě, kdy předem nevíme, kolikrát chceme kód opakovat. Cyklus `while` se opakuje dokud je splněna jeho podmínka (`true`).
```
while(podminka){
    ...Co se ma provest pri kazdem opakovani...
}
```

V následném kódu budeme blikat LEDkou dokud bude TrackJet zapnutý:
```
while(true){
    TrackJet.ledWrite(1, true);
    delay(500);
    TrackJet.ledWrite(1, false);
    delay(500);
}
```

### Cyklus `for`
Cyklus `for` použijeme v případě, kdy dopředu známe, kolikrát chceme kód opakovat. Cyklus `for` má následující formu:
```
for(vytvoreni_promenne; podminka; operace){
    ...Co se ma provest pri kazdem opakovani...
}
```

Oproti cyklu while je zde podmínková část složitější. Skládá se ze 3 částí:
* Vytvoř proměnnou, kterou využiješ v podmínce
* Zadej podmínku, která bude udávat, do kdy máme kód opakovat
* Uprav hodnotu proměnné, pokud je podmínka splněna

Následující program ukazuje, jak bliknout 10x s LED číslo 1 pomocí cyklus `for`.
```
for(int pocet_bliku = 0; pocet_bliku < 10; pocet_bliku++){
    TrackJet.ledWrite(1, true);
    delay(500);
    TrackJet.ledWrite(1, false);
    delay(500);
}
```
Vytvořili jsme proměnnou `pocet_bliku`, která obsahuje celé číslo 0. Dokud je hodnota této proměnné menší než 10, zvýší se její hodnota 1 a provede se kód uvnitř cyklu. Jakmile hodnota proměnné rovna 10, cyklus se ukončí a program pokračuje směrem dolů.

<!---
___
## <a name = funkce>Funkce</a>
**TODO**
-->

___
## <a name = ledky>LEDky</a>
V této kapitole si pořádně ukážeme ovládání LEDek na TrackJet.

Pro ovládání samostatných LED pod panelem TrackJet použijeme funkce:
* `TrackJet.ledWrite(index, state)` - rozsvícení a zhasnutí jedné z led pod panelem TrackJet. Parametr `index` je 1-pravá LED a 2-levá LED. Parametr `state` je 0-nesvítí, 1-svítí.
* `TrackJet.ledWriteAnalog(index, brightness)` - nastavení jasu jedné LED pod panelem TrackJet. Parametr `brightness` je v rozsahu 0-nesvítí až do 100-plně svítí.

Pro ovládání LED na panelu TrackJet použijeme následující funkce:
* `TrackJet.displaySingle(row, col, state);` - rozsvícení a zhasnutí jedné LED na panelu. Parametr `row` udává číslo řádku v rozsahu 0-nahoře po 7-dole. Parametr `col` udává číslo sloupce v rozsahu 0-vlevo po 7-vpravo. Parametr `state` je 0-nesvítí, 1-svítí.
* `TrackJet.displaySingleAnalog(row, col, brightness);` - nastavení jasu jedné LED na panelu. Parametr `row` udává číslo řádku v rozsahu 0-nahoře po 7-dole. Parametr `col` udává číslo sloupce v rozsahu 0-vlevo po 7-vpravo. Parametr `brightness` je v rozsahu 0-nesvítí až do 12-plně svítí.
* `TrackJet.displayAll(brightness)` - nastavení jasu všech LED na panelu. arametr `brightness` je v rozsahu 0-nesvítí až do 12-plně svítí.

Například pro rozsvícení LED na panelu vlevo dole použijeme příkaz:
```
TrackJet.displaySingle(7, 0, true);
```
Stejně tak můžeme pro rozsvícení použít příkaz:
```
TrackJet.displaySingleAnalog(7, 0, 12);
```
___
## <a name = tlacitko>Tlačítko</a>
Nejjednodušším způsobem, jak můžete TrackJet ovládat je pomocí tlačítka **SW1**, které najdete v pravém horním rohu desky elektroniky. Pro zjištění jestli je tlačítko zmáčknuto budeme používat příkaz `TrackJet.buttonRead` v náslející konstrukci.
```
bool tlacitko_zmacknuto = TrackJet.buttonRead();
```
Zde je vytvořena proměnná `tlacitko_zmacknuto` a následně do ní uložen stav tlačítka voláním příkazu `TrackJet.buttonRead`, který nabývá pravdivostní hodnoty `true` nebo `false`.

Příklad: Tento program rozsvítí LED 1 pod panelem při stisku tlačítka SW1.
```
#include "TrackJet/TrackJet.h"

void setup() {
    TrackJet.begin();
}

void loop() {
    if(TrackJet.buttonRead()) {
        TrackJet.ledWrite(1, true);
    }
    else {
        TrackJet.ledWrite(1, false);
    }
}
```

Protože příkaz `TrackJet.buttonRead` nabývá pravdivostní hodnoty `true` nebo `false`, můžeme předchozí program zapsat úsporněji, ale funkčně stejně:
```
#include "TrackJet/TrackJet.h"

void setup() {
    TrackJet.begin();
}

void loop() {
    TrackJet.ledWrite(1, TrackJet.buttonRead());
}
```

___
## <a name = potenciometr>Potenciometr</a>
Dalším způsobem, jak můžete TrackJet ovládat je pomocí potenciometru **RV1**, který najdete v levém horním rohu desky elektroniky. Pro zjištění stavu potenciometru budeme používat příkaz `TrackJet.potentiometerRead`. Tento příkaz vrací hodnotu `0` až `100` podle natočení potenciometru.

Příklad: Tento program řídí jas LED podle natočení potenciometru.
```
#include "TrackJet/TrackJet.h"

void setup() {
    TrackJet.begin();
}

void loop() {
	// Vytvoření celočíselné proměnné
	int jas = 0;
	
	// Přečtení stavu potenciometru (0-100) a uložení do proměnné
	jas = TrackJet.potentiometerRead();
	
	// Nastavení jasu LED1 podle stavu proměnné
	TrackJet.ledWriteAnalog(1, jas);

    delay(100);
}
```

Protože příkaz `TrackJet.potentiometerRead` vrací celočíselnou hodnotu od `0` do `100`, můžeme předchozí program zapsat úsporněji, ale funkčně stejně.
___
## <a name = seriovka>Sériová linka</a>

### Motivace
Při programování robotů se často stane, že potřebujete s programem v robotovi komunikovat. Například když se snažíte odhalit chybu, vypisovat hodnotu senzorů nebo informovat uživatele o ději v programu. Pro tento účel nám poslouží sériová linka.

### Program pro výpis textu na sériové lince
Pro výpis textu na sériové lince budeme používat příkaz `printf`. Abyste na sériové lince jedenkrát vypsali text *Hello World!*, použijte následující program:
```
#include "TrackJet/TrackJet.h"

void setup() {
    TrackJet.begin();
}

void loop() {
    printf("Hello World!\n");
    delay(1000);
}
```
Okolo textu, který chceme vypsat, je třeba vložit dvojité uvozovky `"text"`. Řetězec `\n` označuje znak pro odřádkování, čili obdoba tlačítka *ENTER* v textových editorech. 

### Spuštění sériové linky
1. Po nahrání programu do TrackJet necháme TrackJet zapnutý a připojený USB kabelem k PC.
1. Pomocí tlačítka v levé dolní liště PlatformIO ve tvaru zásuvky spustíme sériovou linku.

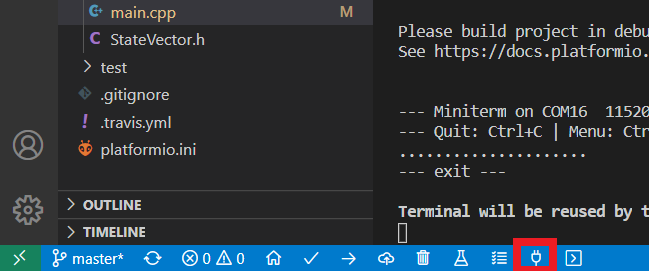
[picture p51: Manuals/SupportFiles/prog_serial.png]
    
1. V monitoru sériové linky v dolní částí okna VS Code najdete příchozí zprávy z TrackJet. Uvidíte, že každou vteřinu přijde nová zpráva ve tvaru *Hello World!*, vždy na novém řádku:
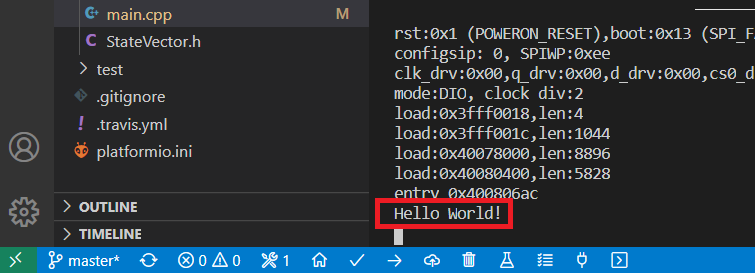
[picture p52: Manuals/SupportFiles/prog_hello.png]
    

### Výpis hodnot proměnných
Často potřebujeme vypsat i hodnotu některé z našich proměnných. V tomto případě můžeme použít takzvaná formátovací direktiva. V textu začínají znakem `%`:
* %d - (decimal) označuje celé číslo
* %f - (float) značí desetinné číslo
* %c - (char) označuje znak
* %s - (string) značí řetězec 

Pro úpravu formátu vypisovaných proměnných máme mnoho dalších možností, které jsou například na [Wiki](https://cs.wikipedia.org/wiki/Printf#Form%C3%A1tovac%C3%AD_%C5%99et%C4%9Bzec). Pro výpis celočíselné proměnné `cele_cislo` do sériové linky použijeme následující příkaz:
```
printf("%d\n", cele_cislo);
```

Příklad: Pro opakovaný výpis času od startu TrackJet použijeme následující program. Hodnota času je uvedena v milisekundách:
```
#include "TrackJet/TrackJet.h"

void setup() {
    TrackJet.begin();
}

void loop() {
    printf("%d\n", millis());
    delay(1000);
}
```
Funkce `millis()` nám vrací počet uplynulých milisekund od startu TrackJet jako celé číslo.

___
## <a name = motory>Motory</a>
Nyní konečně pořádně oživíme TrackJet a začneme s ním jezdit.

Pro řízení motorů můžete použít příkaz `TrackJet.motorSetSpeed(index, speed)`. *index* určuje, který motor ovládáme. Indexy motorů odpovídají popiskům na desce elektroniky. TrackJet disponuje následujícími motory:
* Index 1: motor levého pásu. Točí se na obě strany. Rozsah *speed* -100 až 100 (dopředu). Max. napětí 10V.
* Index 2: motor pravého pásu. Točí se na obě strany. Rozsah *speed* -100 až 100 (dopředu). Max. napětí 10V.
* Index 3: volný konektor. Točí se jednosměrně. Rozsah *speed* 0 až 100. Max. napětí 10V.
* Index 4: volný konektor. Točí se jednosměrně. Rozsah *speed* 0 až 100. Max. napětí 5V.
* Index 5: volný konektor. Točí se jednosměrně. Rozsah *speed* 0 až 100. Max. napětí 10V.
* Index 6: volný konektor. Točí se jednosměrně. Rozsah *speed* 0 až 100. Max. napětí 5V.

Příklad: Následujícími příkazy rozjedeme TrackJet na poloviční rychlost dopředu:
```
TrackJet.motorSetSpeed(1, 50);
TrackJet.motorSetSpeed(2, 50);
```

___
## <a name = enkoder>Enkodér</a>
Enkodérem budeme mírně nepřesně nazývat otočný ovládací prvek podobný potenciometru. Na rozdíl od něj se však otáčí v krocích a umí se točit nepřetržitě dokola. Pro zjištění o kolik kroků byl od startu TrackJet otočen, zavoláme funkci `TrackJet.encoderRead()`. Pokud budeme chtít začít s počítáním kroků od znova, zavoláme funkci `TrackJet.encoderReset()`, která vrátí vracenou hodnotu zpět do nuly. 

Enkodér v sobě integruje další tlačítko. Jeho stav zjistíme zavoláním funkce `TrackJet.encoderReadButton()`, která vrátí *true*, když je zmáčknut a *false* když ne.

___
## <a name = serva>Serva</a>
TrackJet má 3 sloty pro servomotory s indexy:
* Index 1: servo radlice
* Index 2: servo LIDARu
* Index 3: volný konektor

Pro nastavení polohy serva použijeme funkci `TrackJet.servoSetPosition(index, pozice)`, kde *index* popisuje, které servo chceme nastavit, a *pozice* popisuje žádanou polohu serva, čili úhel v rozsahu 0-180.

Standardně jsou serva nastavena na plnou rychlost pohybu, tj. 600°/s. Pokud chceme, aby se pohybovalo pomaleji, můžeme tuto rychlost snižit funkci `TrackJet.servoSetSpeed(index, rychlost)`. Zde *rychlost* značí nastavenou rychlost pohybu serva v rozsahu 0-600°/s.

Pro zjištění aktuální polohy serva je možné použít funkci `TrackJet.servoGetPosition(index)`. Ta vrací číslo udávající aktuální úhel natočení serva *index*. Dále je možné použít funkci `TrackJet.servoMoving(index)`, která vrací *true* když se servo aktuálně pohybuje a *false* když se servo nepohybuje.

___
## <a name = lidar>LIDAR</a>
Pro zjištění měřené vzdálenosti od překážky senzorem LIDAR použijeme funkci `TrackJet.lidarDistance()`. Ta nám vrátí celé číslo udávající počet milimetrů od překážky. 

___
## <a name = panelLed>Výpis textu na LED panel</a>
Pro ukázání jedné celé číslice na panelu TrackJet použijeme funkci `TrackJet.displayDigit(cislo)`, kde *cislo* je celočíselná proměnná v rozsahu 0-9. Pro zobrazení číslice *4* tedy použijeme `TrackJet.displayDigit(4)`.

Pro ukázaní jednoho znaku na panelu TrackJet použijeme funkci `TrackJet.displayChar(znak)`, kde *znak* je proměnná typu *char*. Pro zobrazení znaku *a* tedy použijeme `TrackJet.displayChar('a')`. Tímto způsobem můžeme zobrazovat i číslovky jako v předchozím případě nebo i velká písmena. Přidáním nepovinných parametrů *posunVpravo* a *posunDolu* ve variantě příkazu `TrackJet.displayChar(znak, posunVpravo, posunDolu)` můžeme znak posunovat po obrazovce. Přidané parametry udávají v celých číslech, o kolik LED bude znak posunut.

Pro výpis delšího textu na panel TrackJet slouží funkce `TrackJet.displayText(text)`. Ta postupně vypíše zadaný *text* z proměnné typu *String*. Pro vypsání textu *ahoj* tedy použijeme `TrackJet.displayText("ahoj")`. V základní variantě odjíždí text postupně doleva z panelu. Pro postupné vypsání jednotlivých znaků textu bez posunu přidejte nepovinný binární parametr v hodnotě *false*, tedy `TrackJet.displayText("ahoj", false)`.

Funkce pro postupný výpis více zpráv se bude hodit funkce `TrackJet.displayIsBusy()`. Ta vrací pravdivostní hodnotu (*true* nebo *false*) označující jestli je aktuálně vypisován v minulosti zadaný text.

Příklad: Následující program při startu vypíše text "TrackJet is starting" v pohyblivém módu textu.
```
#include "TrackJet/TrackJet.h"

void setup() {
    TrackJet.begin();
    TrackJet.displayText("TrackJet is starting");
}

void loop() {
    delay(500);
}
```

___
## <a name = buzzer>Bzučák</a>

Pro ovládání bzučáku slouží funkce `TrackJet.soundTone(frekvence)`, kde parametr *frekvence* značí frekvenci zvuku v jednotce Hertz (Hz nebo 1/s). Tento tón bude hrát do té doby, dokud TrackJet nevypnete nebo nezavoláte funkci `TrackJet.soundEnd()`.

Pro tvoření melodie je vhodné použít funkci `TrackJet.soundNote(tón, oktáva)`. Zde je třeba zadat parametr *tón* ve formátu `NOTE_C`, kde měníme poslední písmeno na jiný tón. Druhý parametr *oktáva* udává, ze které oktávy nastavený tón bude.

___
## <a name = cara>Senzor čáry</a>
TrackJet má na své spodní straně 2 infračervené reflexní senzory, které umí měřit světlost povrchu pod ním. To se může hodit když chceme, aby jel TrackJet po čáře. Čára musí být v takovém případě kontrastní k povrchu.

Pro zjištění hodnoty světlosti povrchu zavoláme funkci `TrackJet.lineRead(index)`, kde *index* v hodnotě 1 značí levý senzor a v hodnotě 2 pravý senzor, podobně jako u motorů. Tato funkce vrátí hodnotu v rozsahu 0-100, kde 0 odpovídá tmavšímu povrchu a 100 odpovídá světlejšímu povrchu.

___
## <a name = wifi>WiFi</a>
Pro spuštění WiFi a ovládací webové aplikace slouží funkce `TrackJet.startWiFiCaptain("<your_name>")`. Po jejím zavolání bude postaráno o vytvoření WiFi přístupového bodu (AP) v TrackJet a také o připojní k externí WiFi, jakmile má TrackJet správné přihlašovací údaje a je v dosahu. Také je spuštěn server hostující webovou aplikaci pro dálkové ovládání TrackJet.

___
## <a name = remoteCmd>Vzdálený příkazový řádek</a>
Pro dálkové ovládání TrackJet můžete použít i textové příkazy. Ty budete zadávat do pole *Command entry* na webové stránce dálkového ovládání. Po stisku tlačítka *Enter* (funguje i na klávesnici) je zadaný příkaz odeslán do TrackJet. K použítí přijatého příkazu budeme používat následující funkce:
* `TrackJet.commandGet()` - vrací textový řetězec (proměnnou typu *String*) obsahující aktuálně přijatý příkaz.
* `TrackJet.commandGetIndexed(index)` - vrací textový řetězec obsahující jedno slovo z přijatého příkazu. Slova jsou oddělena mezerami a číslována od 0.
* `TrackJet.commandClear()` - vymaže obsah celého aktuálně přijatého příkazu.

Příklad: Následující program pípne bzučákem na frekvenci 1kHz po 0,5 sekundy po obdržení příkazu "beep":
```
#include "TrackJet/TrackJet.h"

void setup() {
    TrackJet.begin();
    TrackJet.startWiFiCaptain("<your_name>");
}

void loop() {
    if(TrackJet.commandGet() == "beep") {
            TrackJet.soundTone(1000);
            delay(500);
            TrackJet.soundEnd();
            TrackJet.commandClear();  // nutné jinak bude v paměti pořád příkaz "flash" a LED bude pořád svítit
        }
    delay(100);
}
```

Příklad: Následující program spustí bzučák na příkaz "buzzer on" a vypne ho na příkaz "buzzer off":
```
#include "TrackJet/TrackJet.h"

void setup() {
    TrackJet.begin();
    TrackJet.startWiFiCaptain("<your_name>");
}

void loop() {
    if(TrackJet.commandGetIndexed(0) == "buzzer") {
        if(trrCommandGetIndexed(1) == "on") {
            TrackJet.soundTone(1000);
        }
        else if(trrCommandGetIndexed(1) == "off") {
            TrackJet.soundEnd();
        }
        TrackJet.commandClear();
    }
    delay(100);
}
```

TrackJet umožňuje textovou komunikaci i opačným směrem, tedy z TrackJet do webové stránky dálkového ovládání.
* `TrackJet.commandDisp(command)` - odešle textový příkaz *command* z TrackJet a zobrazí ho šedě v poli *Command entry*.

Příklad: Následující program bude v textovém poli *Command entry* vypisovat stav tlačítka TrackJet:
```
#include "TrackJet/TrackJet.h"

void setup() {
    TrackJet.begin();
    TrackJet.startWiFiCaptain("<your_name>");
}

void loop() {
    TrackJet.commandDisp(String(TrackJet.buttonRead()));
    delay(500);
}
```

___
## <a name = odometr>Měření ujeté vzdálenosti</a>
TrackJet je vybaven senzory ujeté vzdálenosti, které nazýváme mírně slangově *enkodéry*. Fungují na principu optické brány, kde je paprsek světla přerušován vnitřními výstupky pásu. Tímto způsobem je možné získat celočíselnou proměnnou, která je zvýšena o 4 při každém posunu pásu o jeden celý segment. Aby enkodéry správně fungovaly, je třeba je zkalibrovat. K tomu je třeba přes vzdálený příkazový řádek zadat `encoder calibrate`. Po zadání bude probíhat kalibrace po dobu 5 sekund. Během této doby je nutné, aby se oba pásy pootočily o několik segmentů. Poté je kalibrace hotova a uložena. 

Celočíselnou proměnnou udávající ujetouo vzdálenost získáme zavoláním funkce `TrackJet.encoderGetSteps(index)`, kde *index* je 1 pro levý pás a 2 pro pravý pás, podobně jako u motorů. 

Pro získání ujeté vzdálenosti daného pásu použijeme funkci `TrackJet.encoderGetDistance(index)`, která nám vrátí ujetou vzdálenost daného pásu vyjádřenou v milimetrech jako desetinné číslo.

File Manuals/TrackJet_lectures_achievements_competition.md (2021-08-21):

V tomto dokumentu se nachází rozpis programovacích lekcí a zadání programovacích úkolů. 

**Programovací lekce** nejsou povinné, ale jsou pro začátečníky velmi vhodné. Zájem o lekci budete vyjadřovat tak, že na svůj řádek v tabulce připíšete na konec číslo lekce, o kterou máte zájem. Jakmile jste lekci absolvovali, číslo zakroužkujete tak, aby bylo jasné, které lekce už jste absolvovali. Účast na lekci je ohodnocena 1 Chotěcoinem,

**Programovací úkoly** jsou úkoly, které budete řešit samostatně. Ke každému úkolu potřebujete soubor znalostí, který je obsažen v některých z lekcí. Úkoly je však možné řešit i jen pomocí programovacího manuálu (pro pokročilé). Splnění úkolu bude kontrolovat vedoucí a odmění ho 2 Chotěcoiny. Po splnění úkolu si v tabulce na vašem řádku zaznačte křížkem jeho splnění. 

# Lekce 0
Zprovozníme programovací prostředí VS Code + PlatformIO tak, abyste mohli nahrát kód do TrckJet z vašeho PC.

# Lekce 1
Rozblikáme LED pod panelem na TrackJet.

## Úkol 1 - Blikání LED
Napište program, který bude rychle blikat zelenou LED (LED1, vpravo pod panelem). Doba svícení je 200 ms. Doba zhasnutí je 200 ms.

## Úkol 2 - Záblesky LED
Napište program, který každou vteřinu krátce zableskne LED1. Délka svícení je 50 ms. LED se zableskne každou vteřinu.

## Úkol 3 - Železniční přejezd
Napište program, který bude blikat jako železniční přejezd. Při blikání se střídají alespoň 2 různé světla **na LED panelu**. Délka svícení je volitelná.

# Lekce 2
Přečteme stav tlačítka, ukážeme si binární proměnnou.

## Úkol 4 - Manuální blikání LED
Napište program, který bliká libovolnou LED pouze při stisknutém tlačítku SW2. Doba svícení je 200 ms. Doba zhasnutí je 200 ms.

## Úkol 5 - Stabilní stav LED
Napište program, který bude tlačítkem zapínat a vypínat libovolnou LED.
Po stisku tlačítka SW2 zůstane LED zapnutá. Po opětovném zmáčknutí tačítka se LED vypne.

# Lekce 3
Přečteme stav potenciometru, ukážeme si číselnou proměnnou a nastavíme jas LED.

## Úkol 6 - Rychlost blikání
Napište program, který bude blikat libovolnou LED a rychlost tohoto blikání bude nastavitelná pomocí natočení potenciometru.

# Lekce 4
Roztočíme motory a ukážeme si podmínku "if".

## Úkol 7 - Otáčení motoru dopředu a dozadu
Napiště program, který bude pomocí potenciometru ovládat jeden z motorů tak, aby mohl jezdit na obě strany. V prostřední poloze potenciometru bude tedy motor stát.

## Úkol 8 - Jízda vpřed/vzad
Napište program, který bude jezdit s TrackJet dopředu a dozadu. Doba jízdy dopředu je 1 s, dozadu taky 1 s. Rychlost je libovolná nenulová.

## Úkol 9 - Nastavení jasu LED po stisku tlačítka
Napište program, který nastavý jas libovolné LED podle polohy potenciometru. Nastavení jasu proběhne **jen** po stisku tlačítka SW2. Když není zmáčknuto, je jas stabilní.

# Lekce 5
TrackJet začne komunikovat s počítačem pomocí sériové linky.

## Úkol 10 - Vypsání hodnoty potenciommetru
Napiště program, který bude na sériovou linku vypisovat hodnotu natočení potenciometru.

## Úkol 11 - Vysání času od startu TrackJet bez funkce millis()
Napište program, který bude vypisovat celočíselnou proměnnou každou vteřinu. Tuto proměnnou však každou milisekundu zvyšte o 1. Je chování tohoto programu stejné jako v případě použití funkce `millis()`?

# Lekce 6
Přečteme stav rotačního enkodéru a rozpohybujeme servomotory.

## Úkol 11 - Vypsání stavu enkodéru
Napište program, který na sériovku vypíše akutální hodnotu rotačního enkodéru. Po stisku tlačítku tuto hodnotu resetujte do nuly.

## Úkol 12 - Nastavení polohy serva podle potenciometru
Napište program, který přečte polohu potenciometru a podle ní nastaví polohu libovolného serva.

## Úkol 13 - Mávání servem
Napište program, který nastaví rychlost serva 2 (LIDAR) na **polovinu** jeho maximální rychlosti. Touto rychlostí jezděte se servem periodicky mezi krajmíni polohami.

# Lekce 7
Budeme měřit vzdálenost mezi překážkou a TrackJet pomocí senzoru LIDAR.

## Úkol 14 - Parkovací senzory
Napište program, který bude na sériovou linku posílat sekvenci znaků tak dlouhou, kolik desítek centimetrů je mezi LIDAR senzorem a překážkou. Např. při měření vzdálenosti 40 cm bude program vypisovat na jedden řádek eskvenci `####`. 

## Úkol 15 - Držení si odstupu
Napište program, který zajistí, že si TrackJet bude udržovat odstup od překážky (ruky programátora) na vzdálenost 30 cm. Když je vzdálenost větší, pojede dopředu a když menší, bude couvat. Pozor, aby nezačal kmitat, nemusí být udržovaná vzdálenost úplně přesná.

# Lekce 8
Rozezníme bzučák na TrackJet a ukážeme si jak nastavit jeho frekvenci na konkrétní tóny.

## Úkol 16 - Hraní melodie
Napište program, který zahraje vaši oblíbenou melodii (oblíbená píseň, film, opera) nebo jakoukoliv jinou melodii o alespoň 5 notách.

## Úkol 17 - Klakson
Napište program, který *zatroubí* bzučákem v případě, že je čtení vzdálenosti z LIDARu menší než 5 cm.

## Úkol 18- Theremin
Napište program, který bude číst vzdálenost od překážky z LIDARu a podle této vzdálenosti bude nastavovat frekvenci bzučáku. Zahrejte vedoucímu hezkou melodii.

# Lekce 9
Ukážeme si spuštění WiFi knihovny a použití vzdáleného příkazového řádku.

## Úkol 19 - Vzdálené měření vzdálenosti
Napište program, který po zadání příkazu "dist" do vzdáleného příkazového řádku vrátí měřenou vzdálenost od překážky LIDARem.

# Lekce 10
Rozblikáme LED bez použití příkazu delay(). Ukážeme si cyklus.

## Úkol 20 - Vlna
Napište program, který bude postupně vyblikávat všechny LEDky v jednom řádku LED panelu. Vždy svítí jen jedna LED.

## Úkol 21 - K.I.T.T.
Napište program, který bude postupně vyblikávat všechny LEDky v jednom řádku LED panelu. Vlna se bude symstricky zpět. Vždy svítí jen jedna LED. Blikání bude připomínat vzor na [slavném inteligentním autě K.I.T.T.](https://www.youtube.com/watch?v=oNyXYPhnUIs&ab_channel=NBCClassics).

# Lekce 11
Změříme ujetou vzdálenost pomocí *enkodérů*. Ty měří pohyb pásů. K úspěšnému měření je třeba enkodéry zkalibrovat.

## Úkol 22 - Změření metru
Napište program, který po zmáčknutí tlačítka rozjede TrackJet směrem dopředu libovolnou rychlostí. Po ujetí 1 metru se TrackJet zastaví.

## Úkol 23 - Autonomní jízda
Napište program, který bude s TrackJet jezdit po prostoru. Při detekování překážky LIDARem se TrackJet zastaví. Otočí a pokračuje v jízdě.

## Úkol 24 - Autonomní jízda s rozhlížením
Napište program, který vylepší autonomní jízdu z minulého úkolu o *rozlížení*. Při detekování překážky TrackJet zastaví, rozhlédne se do stran pomocí serva natáčejího LIDAR senzor. Program vybere nejvhodnější směr pro další jízdu. Tam se TrackJet otočí a rozjede.

## Úkol 25 - Otočení o zadaný úhel
Napište program, který bude číst kroky otočení rotačního enkodéru a podle nich bude na LED panelu zobrazovat linku svítících LED. Tato linka bude vždy začínat ve středu panelu a může být natočena v 8 možných úhlech (0, 45, 90, 135, 180, 225, 270, 315)°. Po stisku tlačítka enkodéru se TrackJet začne otáčet. Otočí se o zadaný úhel co nejpřesněji.

## Bonusové úkoly

1. Napiš program, který postupně rozsvítí všechny LED v matici v obou
        diagonálách. Nesmí být zapnuto více LED současně.

2. Program, který postupně rozsvítí každou LED v matici za použití dvou for
        cyklů. Nesmí být zapnuto více LED současně.

3. Program, kde je rozsvícená taková LED v sloupci, jaká je vzdálenost před 
        LiDAR senzorem(Jak je v originálním programu)

4. Program, který na zmáčknutí tlačítka vypíše procento naplnění baterie
        na sériovou linku, na druhé zmáčknutí vypíše napětí.

5. Program, který na každé otočení enkodéru posune servem o 10% jeho rozsahu. 
        Když už nebude možnost hýbat se dál do tohoto směru, servo se natočí
        na druhou stranu a nechá uživatele pokračovat, vypíše ale na sériovou
        linku informaci o resetování polohy serva.
        
6. Program, kde na matici svítí první LED, a po každém otočení enkodéru
        se rozsvítí ta vedle ní atd., než matice přeteča a rozsvítí se LED
        na dalším řádku.

# Soutěže

## Tour de Chotěborky [dálkové ovládání]
Úkolem je s robotem pomocí dálkového ovládání projet zadanou trasu v Chotěborkách v co nejkratším čase. Trasa je zadána vedoucími, ti dohlíží na její projetí a měří čas. Časová penalizace za každý dotyk člověka a robota je 15 sekund. Nejsou penalizovány případy, ve kterých selže technika. V takovém případě se zastavuje časomíra. Vyhraje robot, který projede zadanou trasu nejrychleji.

Bodování od porvního místa: 20, 18, 16, 14, 13, 12, 11, 10, 9, 8, 8, ...

## Úklid tábora [dálkové ovládání]
Úkolem je s robotem pomocí dálkového ovládání uklidit vymezený prostor od nepořádku (3D tištěné *puky*). Za uklizený se počítá puk, který je celým tělem mimo vymezený prostor. Vyhraje robot, který uklidí vymezený prostor nejrychleji.

Bodování od porvního místa: 20, 18, 16, 14, 13, 12, 11, 10, 9, 8, 8, ...

## Velký závod [dálkové ovládání]
Úkolem je s robotem pomocí dálkového ovládání projet zadanou trasu rychleji než soupeři. Při závodě soutěží několik robotů zaráz.

Bodování od porvního místa: 14, 12, 10, 8.

## Úniková hra [autonomní]
Úkolem je, aby robot našel východ z čtvercového hřiště a projel jím ven co nejrychleji. Hřiště je ohraničeno stěnou, která je detekovatelná senzorem vzdálenosti LIDAR. Robot startuje uprostřed hřiště a je náhodně natočen. Měření času je ukončeno až je celým tělem mimo hřiště. Vyhraje robot, který najde cestu z hřiště nejrychleji.

Bodování od porvního místa: 25, 23, 21, 19, 17, 15, 15, ...

## Jízda podél stěny [autonomní]
Úkolem je, aby robot co nejrychleji autonomně projel zadanou trasu. K navigaci slouží stěny po straně trasy, od kterých lze měřit vzdálenost LIDAR senzorem. 

Bodování od porvního místa: 25, 23, 21, 19, 17, 15, 15, ...

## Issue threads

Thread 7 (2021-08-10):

Fix servo linear mode

MarPta, 2021-08-10:

Closed 2021-08-12.

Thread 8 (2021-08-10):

Manual fixes

petrVavra, 2021-08-10:
Dofotit a dopsat
- pájení switche SW2
- vytočení serva radlice do maximální polohy

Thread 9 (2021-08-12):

Electronics manual fix

coufy, 2021-08-12:
Vynechat pájení 1206 v návodu elektro

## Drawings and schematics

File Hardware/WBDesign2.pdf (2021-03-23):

## WEBENCH ® Design Report

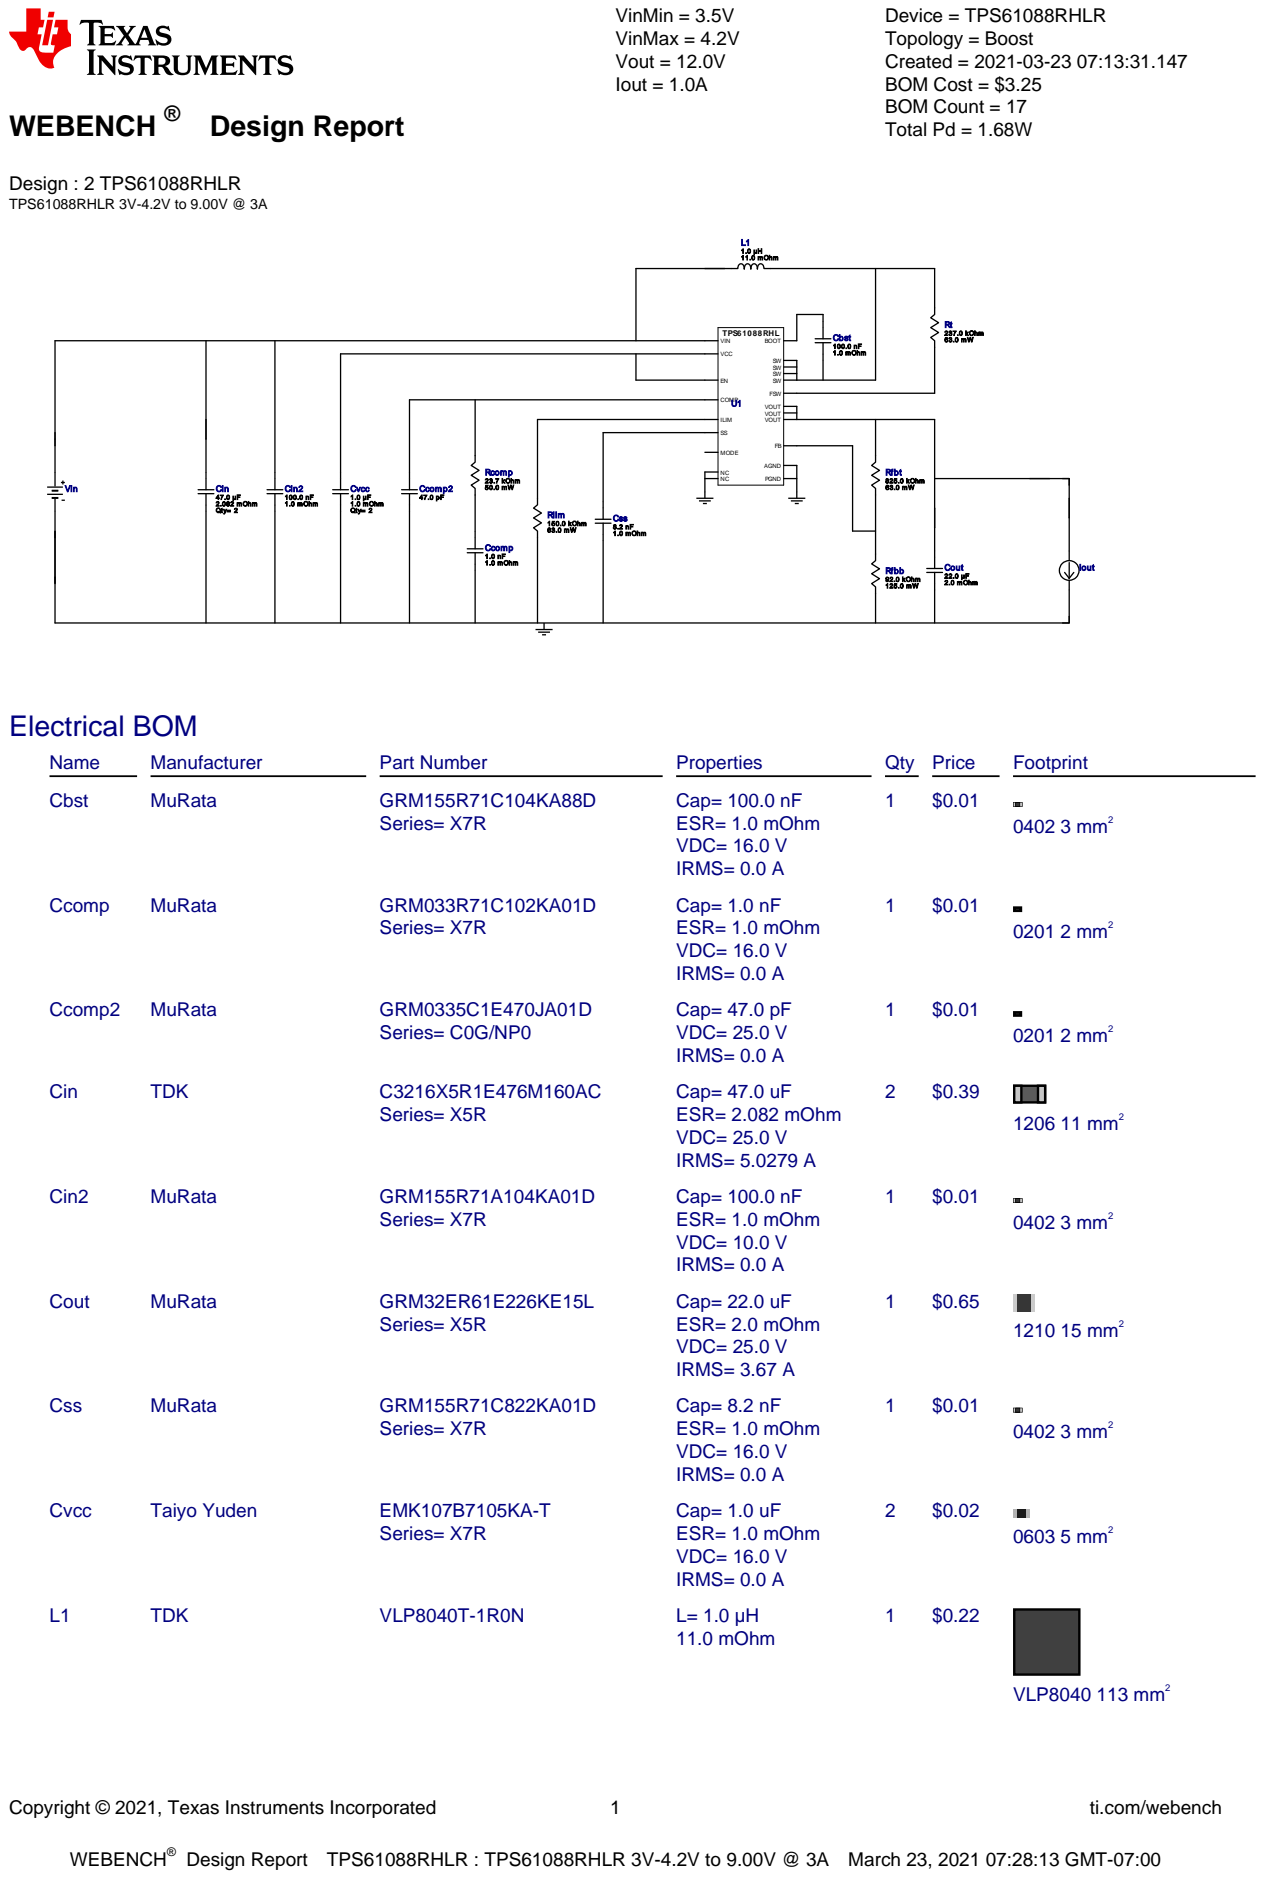
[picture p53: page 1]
Copyright © 2021, Texas Instruments Incorporated; ti.com/webench; WEBENCH®; Design : 2 TPS61088RHLR TPS61088RHLR 3V-4.2V to 9.00V @ 3A; VinMin = 3.5V VinMax = 4.2V Vout = 12.0V Iout = 1.0A; Device = TPS61088RHLR Topology = Boost Created = 2021-03-23 07:13:31.147 BOM Cost = $3.25 BOM Count = 17 Total Pd = 1.68W; Rlim 150.0 kOhm 63.0 mW; Ccomp 1.0 nF 1.0 mOhm; Cin2 100.0 nF 1.0 mOhm; TPS61088RHL; VCC; FSW; VIN; BOOT; MODE; VOUT VOUT VOUT; COMP; ILIM; AGND; PGND; Rfbt 825.0 kOhm; Rt 237.0 kOhm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

Design Report TPS61088RHLR : TPS61088RHLR 3V-4.2V to 9.00V @ 3A March 23, 2021 07:28:13 GMT-07:00

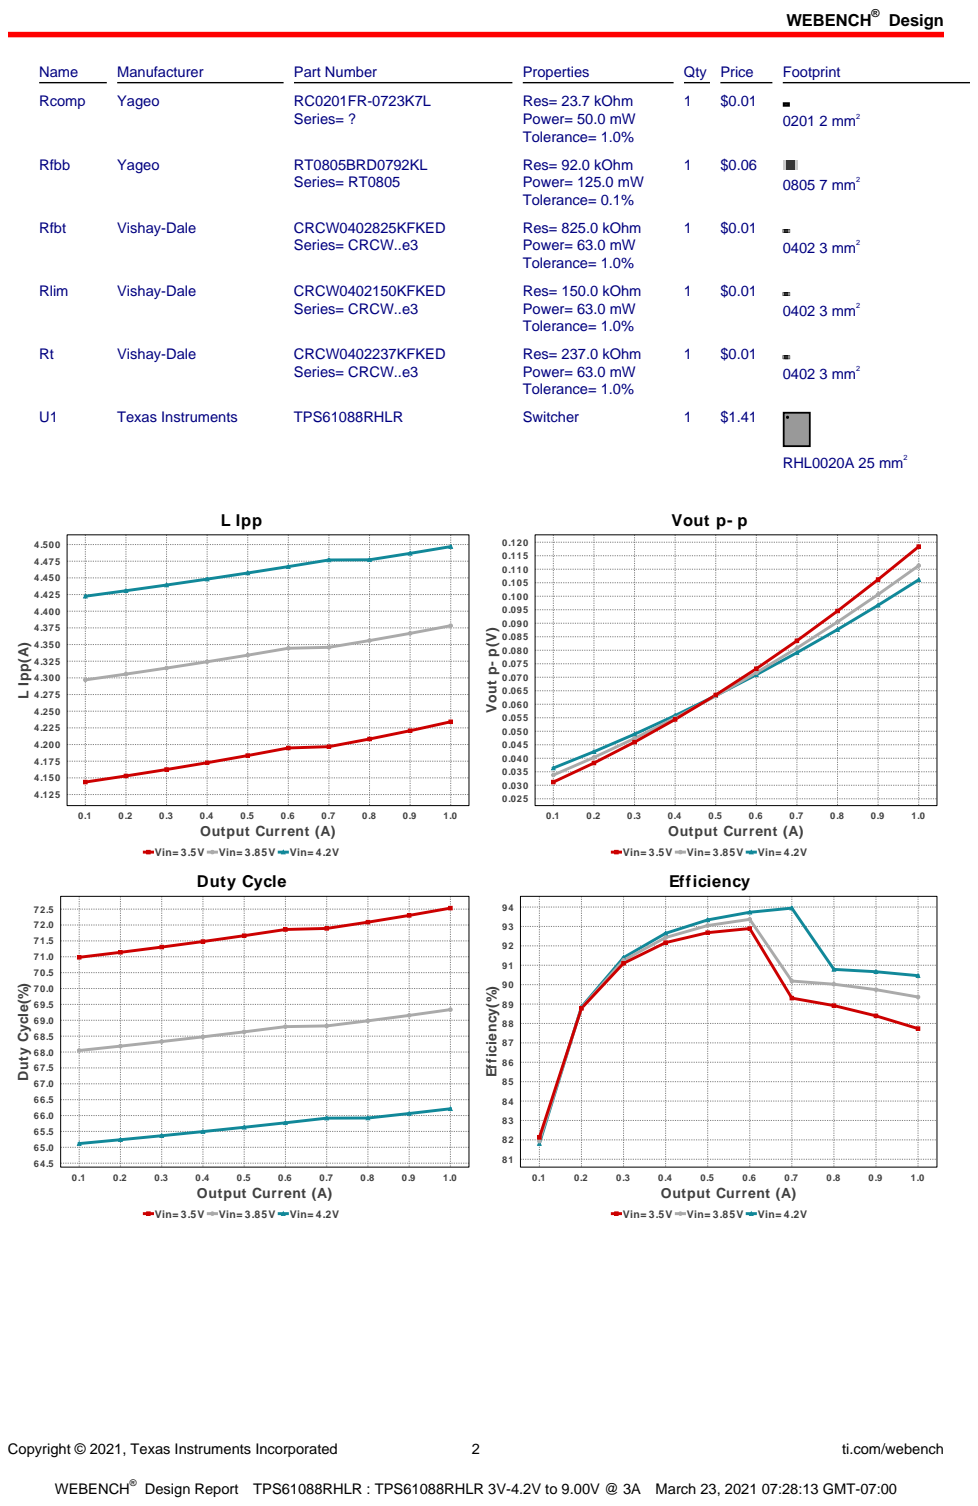
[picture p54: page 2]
Design; Copyright © 2021, Texas Instruments Incorporated; ti.com/webench; Name; Manufacturer; Part Number; Properties; Qty Price; Footprint; Rcomp; Yageo; Series= ?; Res= 23.7 kOhm Power= 50.0 mW Tolerance= 1.0%; 0201 2 mm²; Rfbb; RT0805BRD0792KL; Series= RT0805; Res= 92.0 kOhm Power= 125.0 mW Tolerance= 0.1%; 0805 7 mm²; Rfbt; Vishay-Dale; CRCW0402825KFKED; Series= CRCW..e3; Res= 825.0 kOhm Power= 63.0 mW Tolerance= 1.0%; 0402 3 mm²; Rlim; CRCW0402150KFKED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

Vin= 3.5V Vin= 3.85V Vin= 4.2V
Duty Cycle

Efficiency

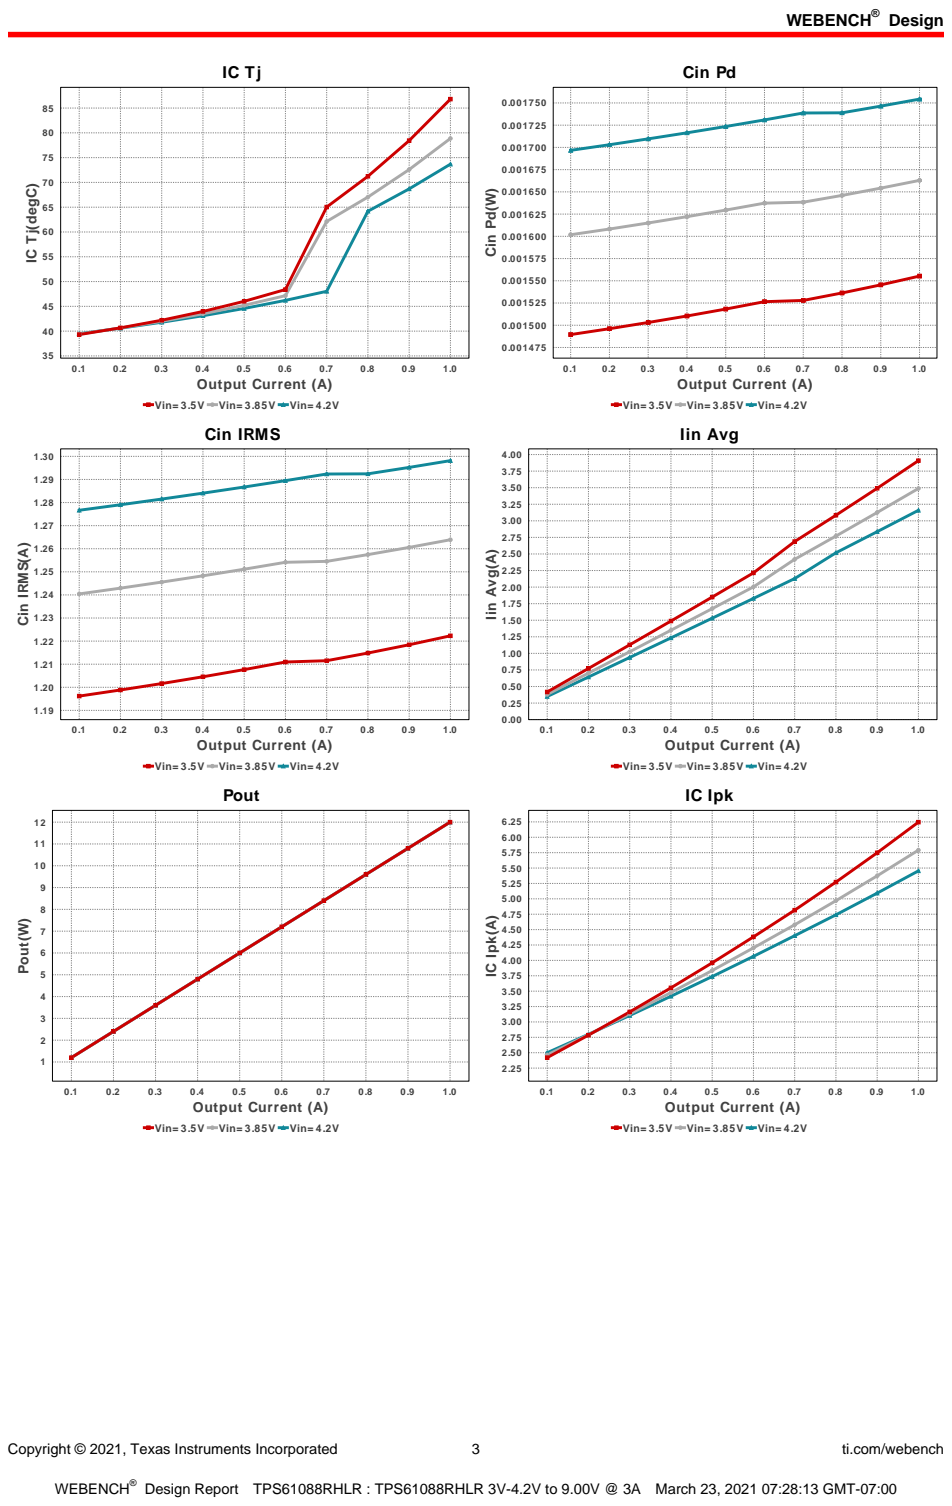
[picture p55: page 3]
Copyright © 2021, Texas Instruments Incorporated; ti.com/webench; 1.0 Output Current (A); Cin Pd; Cin Pd(W); Cin IRMS(A); Iin Avg(A); Pout; Pout(W); IC Ipk; IC Ipk(A)

IC Tj(degC)

Vin= 3.5V Vin= 3.85V Vin= 4.2V
Cin IRMS

Iin Avg

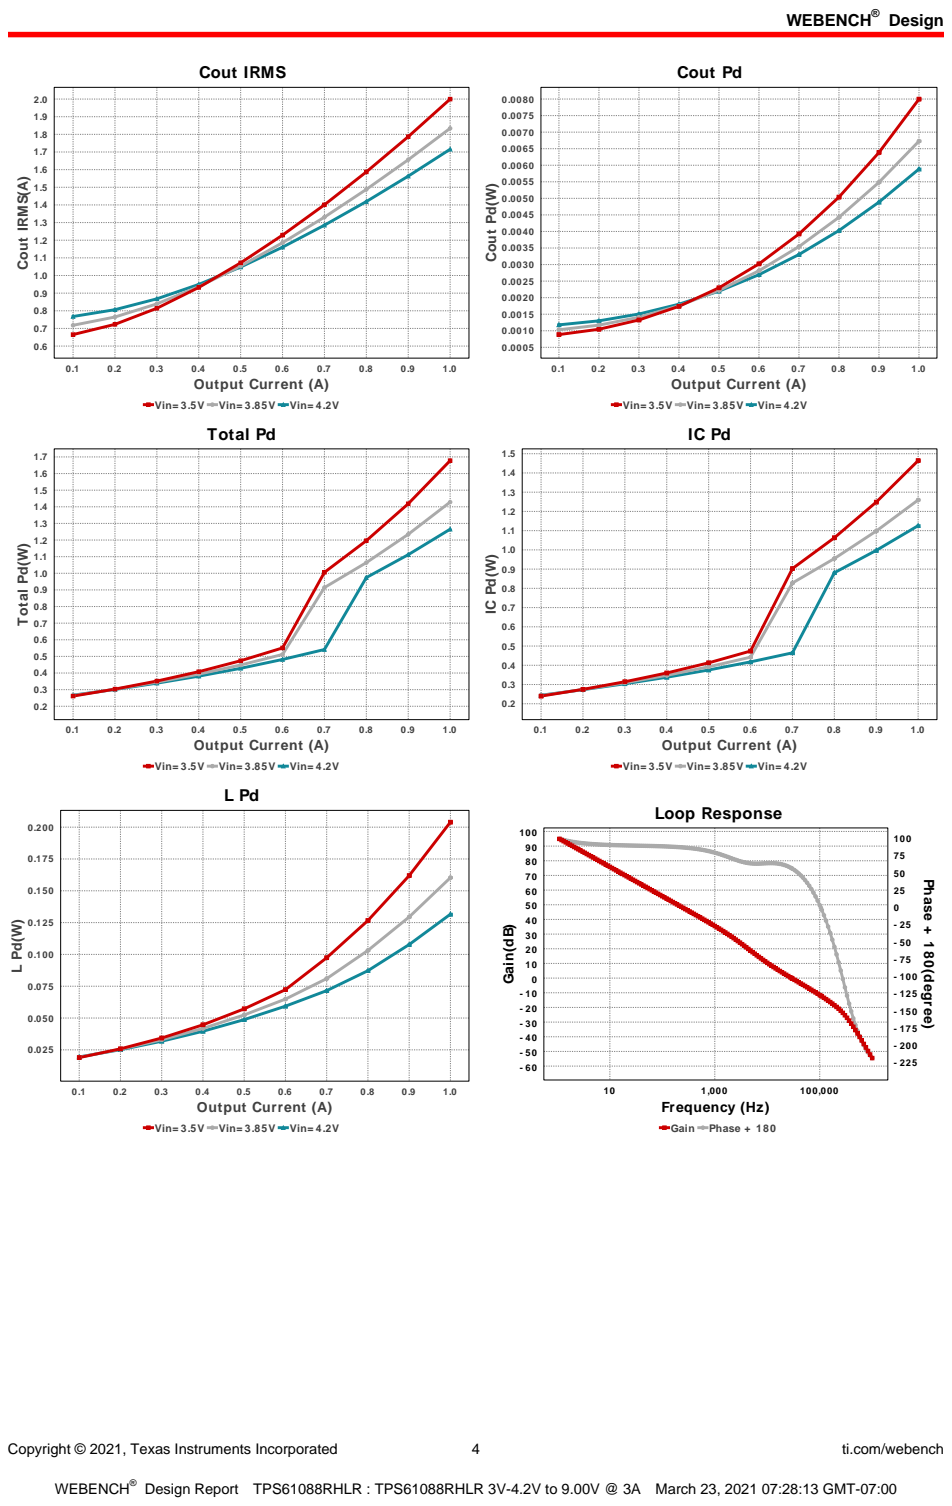
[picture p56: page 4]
Copyright © 2021, Texas Instruments Incorporated; ti.com/webench; Cout IRMS; 1.0 Output Current (A); Cout IRMS(A); Cout Pd; Cout Pd(W); Total Pd(W); Loop Response; Gain Phase + 180; 100,000 Frequency (Hz); Gain(dB); Phase + 180(degree)

Vin= 3.5V Vin= 3.85V Vin= 4.2V
Total Pd

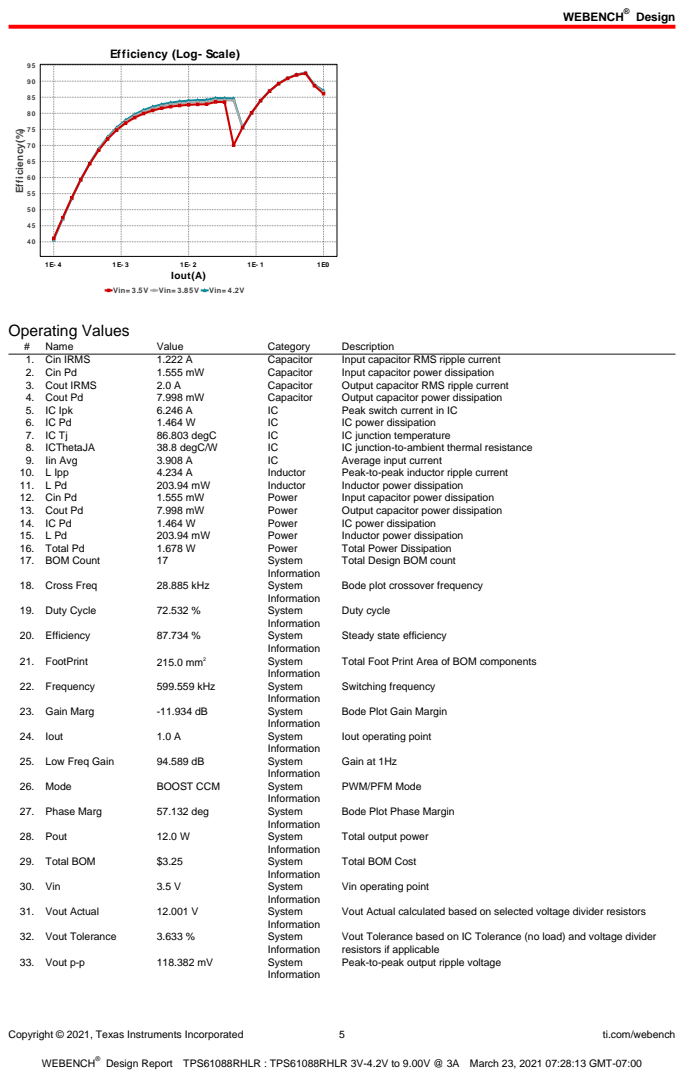
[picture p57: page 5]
Copyright © 2021, Texas Instruments Incorporated; ti.com/webench; Iout(A); Efficiency(%); Operating Values; Name; Value; Category; Description; 1. Cin IRMS; Capacitor; Input capacitor RMS ripple current; 2. Cin Pd; Input capacitor power dissipation; 3. Cout IRMS; Output capacitor RMS ripple current; 4. Cout Pd; Output capacitor power dissipation; 5. IC Ipk; Peak switch current in IC; IC power dissipation; 86.803 degC; IC junction temperature; 8. ICThetaJA; 38.8 degC/W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

Efficiency (Log- Scale)

Vin= 3.5V Vin= 3.85V Vin= 4.2V

Total Design BOM count

Bode plot crossover frequency

Steady state efficiency

Total Foot Print Area of BOM components

Bode Plot Gain Margin

Iout operating point

PWM/PFM Mode

Bode Plot Phase Margin

Total output power

Total BOM Cost

Vin operating point

Vout Actual calculated based on selected voltage divider resistors

Vout Tolerance based on IC Tolerance (no load) and voltage divider
resistors if applicable
Peak-to-peak output ripple voltage

Copyright © 2021, Texas Instruments Incorporated | 6 | ti.com/webench

## Design Inputs

Name | Value | Description
Iout | 1.0 | Maximum Output Current
VinMax | 4.2 | Maximum input voltage
VinMin | 3.5 | Minimum input voltage
Vout | 12.0 | Output Voltage
base_pn | TPS61088 | Base Product Number
source | DC | Input Source Type
Ta | 30.0 | Ambient temperature


Copyright © 2021, Texas Instruments Incorporated | 7 | ti.com/webench

## Assembly

## Component Testing

Some published data on components in datasheets such as Capacitor ESR and Inductor DC resistance is based on conservative values that will guarantee that the components always exceed the specification. For design purposes it is usually better to work with typical values. Since this data is not always available it is a good practice to measure the Capacitance and ESR values of Cin and Cout, and the inductance and DC resistance of L1 before assembly of the board. Any large discrepancies in values should be electrically simulated in WEBENCH to check for instabilities and thermally simulated in WebTHERM to make sure critical temperatures are not exceeded.
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

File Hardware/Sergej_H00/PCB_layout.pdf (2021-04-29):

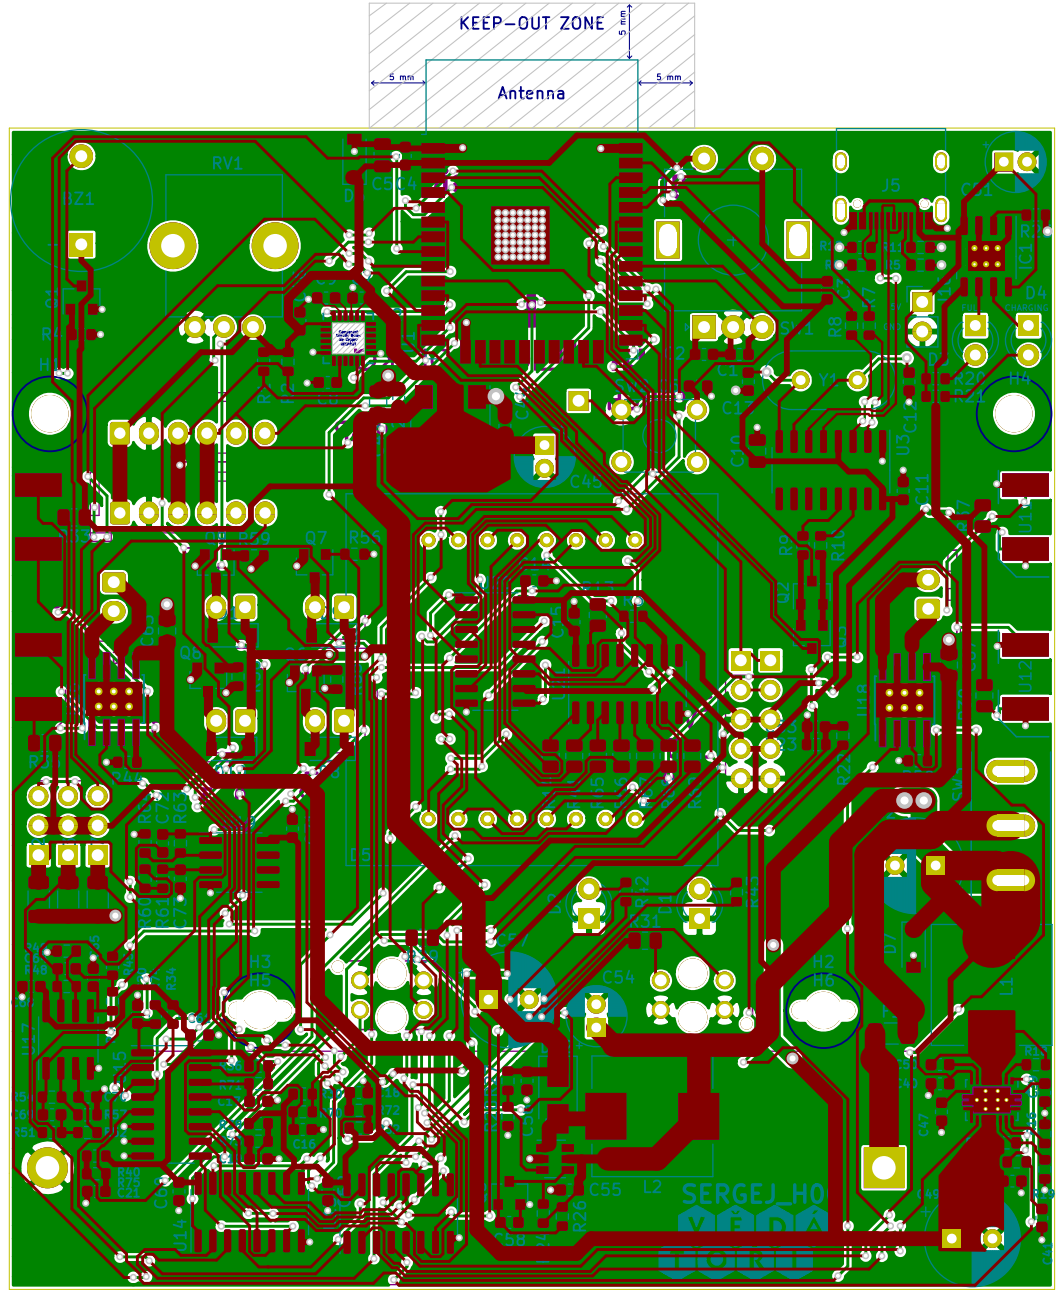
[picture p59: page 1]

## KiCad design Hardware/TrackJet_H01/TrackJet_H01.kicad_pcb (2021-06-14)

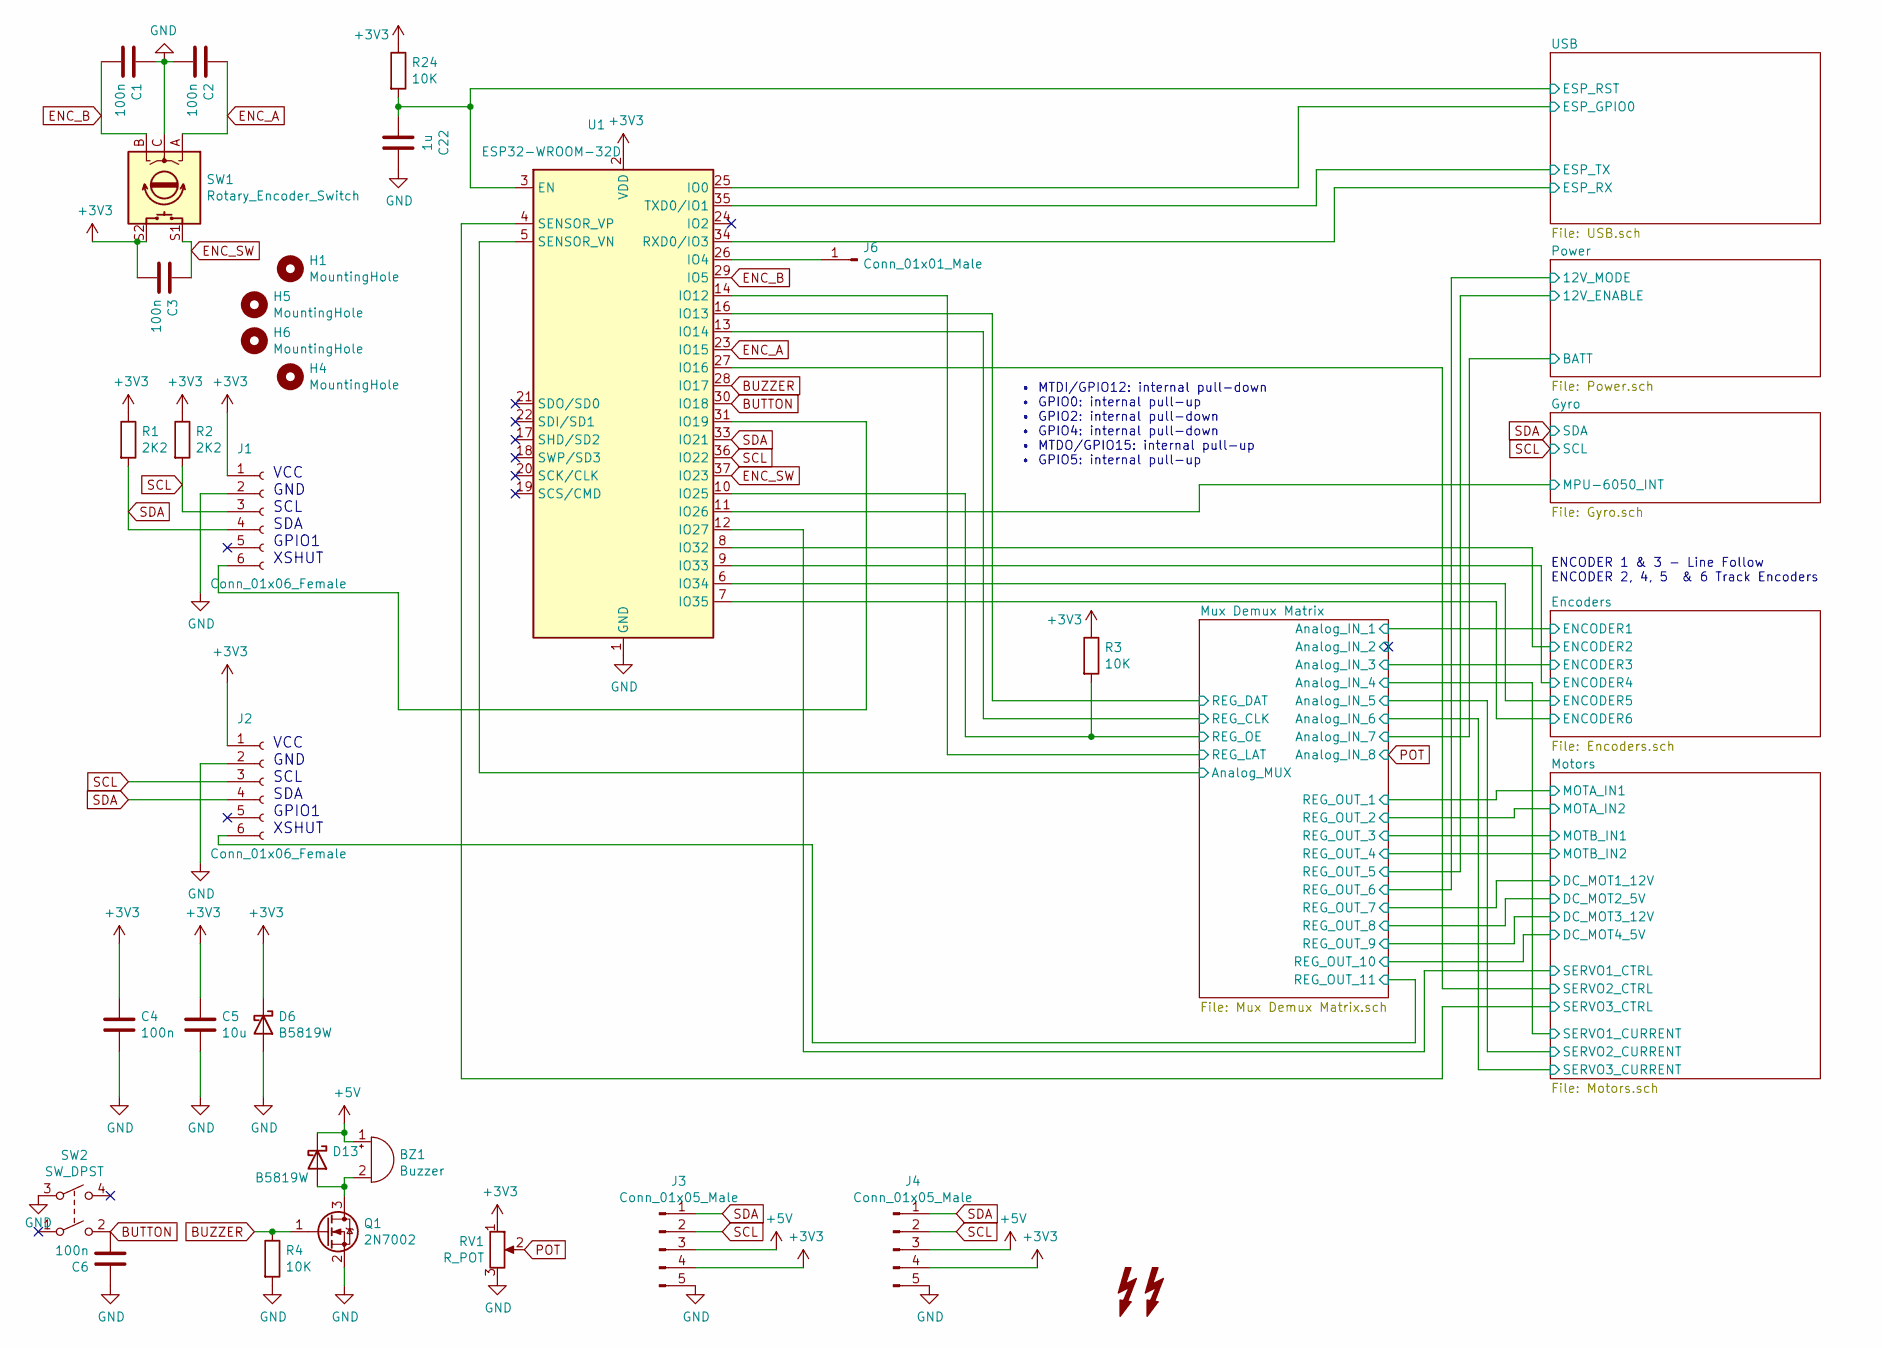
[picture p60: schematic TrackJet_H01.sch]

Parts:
BZ1: Buzzer; Buzzer_12x9.5RM7.6
C1, C2, C3, C4, C6: 100n; C_0603_1608Metric; LCSC C14663
C5: 10u; C_0805_2012Metric; LCSC C15850
C22: 1u; C_0603_1608Metric; LCSC C15849
D6, D13: B5819W; D_SOD-123; LCSC C8598
G1: LOGO; Coufal_elektronika_text_30x13mm
G2: LOGO; Vedatori_15mm
H1, H4: MountingHole; MountingHole_3.2mm_M3
H5, H6: MountingHole; ZIP_Tie_Slot_Hole
J1, J2: Conn_01x06_Female; JST_XH_B6B-XH-A_1x06_P2.50mm_Vertical
J3, J4: Conn_01x05_Male; PinHeader_1x05_P2.54mm_Vertical
J6: Conn_01x01_Male; PinHeader_1x01_P2.54mm_Vertical
Q1: 2N7002; SOT-23; LCSC C8545
R1, R2: 2K2; R_0603_1608Metric; LCSC C4190
R3, R4, R24: 10K; R_0603_1608Metric; LCSC C25804
RV1: R_POT; Potentiometer_Alps_RK09K_Single_Vertical
SW1: Rotary_Encoder_Switch; RotaryEncoder_Alps_EC11E-Switch_Vertical_H20mm
SW2: SW_DPST; SW_TH_Tactile_Omron_B3F-10xx
U1: ESP32-WROOM-32D; ESP32-WROOM-32; LCSC C473012

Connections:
+3V3: C3.2, C4.1, C5.1, D6.1 (K), J1.1, J2.1, J3.4, J4.4, R1.1, R2.1, R3.1, R24.1, RV1.1, SW1.S2, U1.2 (VDD); also elsewhere on the board
+5V: BZ1.1 (-), D13.1 (K), J3.3, J4.3; also elsewhere on the board
/Encoders/ENCODER2: U1.8 (IO32); also elsewhere on the board
/Encoders/ENCODER4: U1.9 (IO33); also elsewhere on the board
/Encoders/ENCODER5: U1.6 (IO34); also elsewhere on the board
/Encoders/ENCODER6: U1.7 (IO35); also elsewhere on the board
/Gyro/MPU-6050_INT: U1.11 (IO26); also elsewhere on the board
/Motors/SERVO1_CTRL: U1.12 (IO27); also elsewhere on the board
/Motors/SERVO2_CTRL: U1.27 (IO16); also elsewhere on the board
/Motors/SERVO3_CTRL: U1.4 (SENSOR_VP); also elsewhere on the board
/Mux Demux Matrix/Analog_MUX: U1.5 (SENSOR_VN); also elsewhere on the board
/Mux Demux Matrix/REG_CLK: U1.13 (IO14); also elsewhere on the board
/Mux Demux Matrix/REG_DAT: U1.16 (IO13); also elsewhere on the board
/Mux Demux Matrix/REG_LAT: U1.14 (IO12); also elsewhere on the board
/Mux Demux Matrix/REG_OE: R3.2, U1.10 (IO25); also elsewhere on the board
/Mux Demux Matrix/REG_OUT_11: J2.6; also elsewhere on the board
/USB/ESP_GPIO0: U1.25 (IO0); also elsewhere on the board
/USB/ESP_RST: C22.2, R24.2, U1.3 (EN); also elsewhere on the board
/USB/ESP_RX: U1.34 (RXD0/IO3); also elsewhere on the board
/USB/ESP_TX: U1.35 (TXD0/IO1); also elsewhere on the board
BUTTON: C6.2, SW2.2, U1.30 (IO18)
BUZZER: Q1.1 (G), R4.1, U1.28 (IO17)
ENC_A: C2.1, SW1.A, U1.23 (IO15)
ENC_B: C1.2, SW1.B, U1.29 (IO5)
ENC_SW: C3.1, SW1.S1, U1.37 (IO23)
GND: C1.1, C2.2, C4.2, C5.2, C6.1, C22.1, D6.2 (A), J1.2, J2.2, J3.5, J4.5, Q1.2 (S), R4.2, RV1.3, SW1.C, SW2.3, U1.1 (GND), U1.15 (GND), U1.38 (GND), U1.39 (GND); also elsewhere on the board
unnamed: BZ1.2 (+), D13.2 (A), Q1.3 (D)
unnamed: J1.6, U1.31 (IO19)
unnamed: J6.1, U1.26 (IO4)
POT: RV1.2; also elsewhere on the board
SCL: J1.3, J2.3, J3.2, J4.2, R2.2, U1.36 (IO22); also elsewhere on the board
SDA: J1.4, J2.4, J3.1, J4.1, R1.2, U1.33 (IO21); also elsewhere on the board

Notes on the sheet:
VCC GND SCL SDA GPIO1 XSHUT
• MTDI/GPIO12: internal pull-down • GPIO0: internal pull-up • GPIO2: internal pull-down • GPIO4: internal pull-down • MTDO/GPIO15: internal pull-up • GPIO5: internal pull-up
ENCODER 1 & 3 - Line Follow ENCODER 2, 4, 5 & 6 Track Encoders

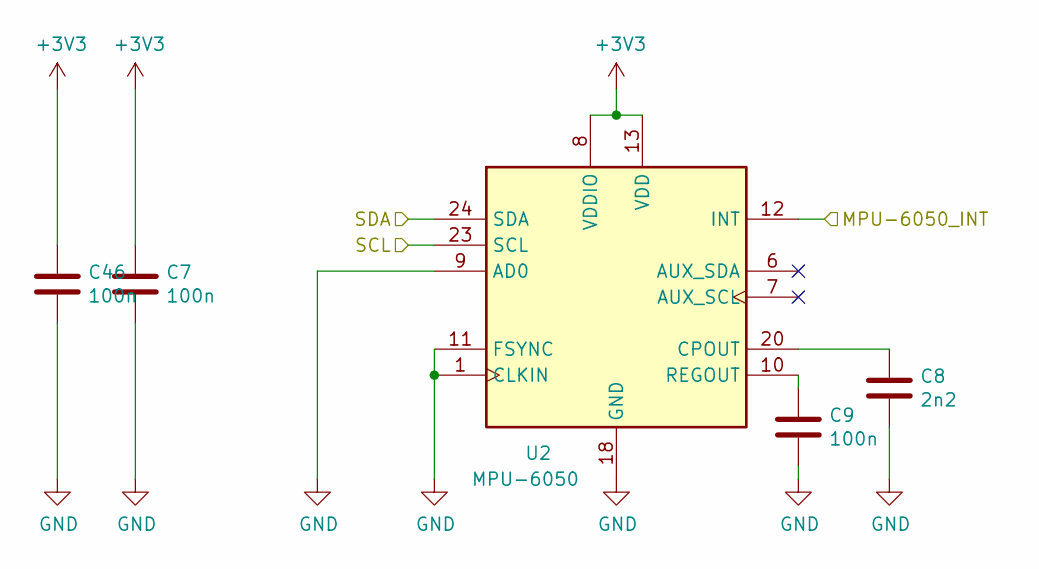
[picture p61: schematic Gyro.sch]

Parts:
C7, C9, C46: 100n; C_0603_1608Metric; LCSC C14663
C8: 2n2; C_0603_1608Metric; LCSC C1604
U2: MPU-6050; InvenSense_QFN-24_4x4mm_P0.5mm; LCSC C24112

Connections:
+3V3: C7.1, C46.1, U2.8 (VDDIO), U2.13 (VDD); also elsewhere on the board
/Gyro/MPU-6050_INT: U2.12 (INT); also elsewhere on the board
GND: C7.2, C8.2, C9.2, C46.2, U2.1 (CLKIN), U2.9 (AD0), U2.11 (FSYNC), U2.18 (GND); also elsewhere on the board
unnamed: C8.1, U2.20 (CPOUT)
unnamed: C9.1, U2.10 (REGOUT)
SCL: U2.23 (SCL); also elsewhere on the board
SDA: U2.24 (SDA); also elsewhere on the board

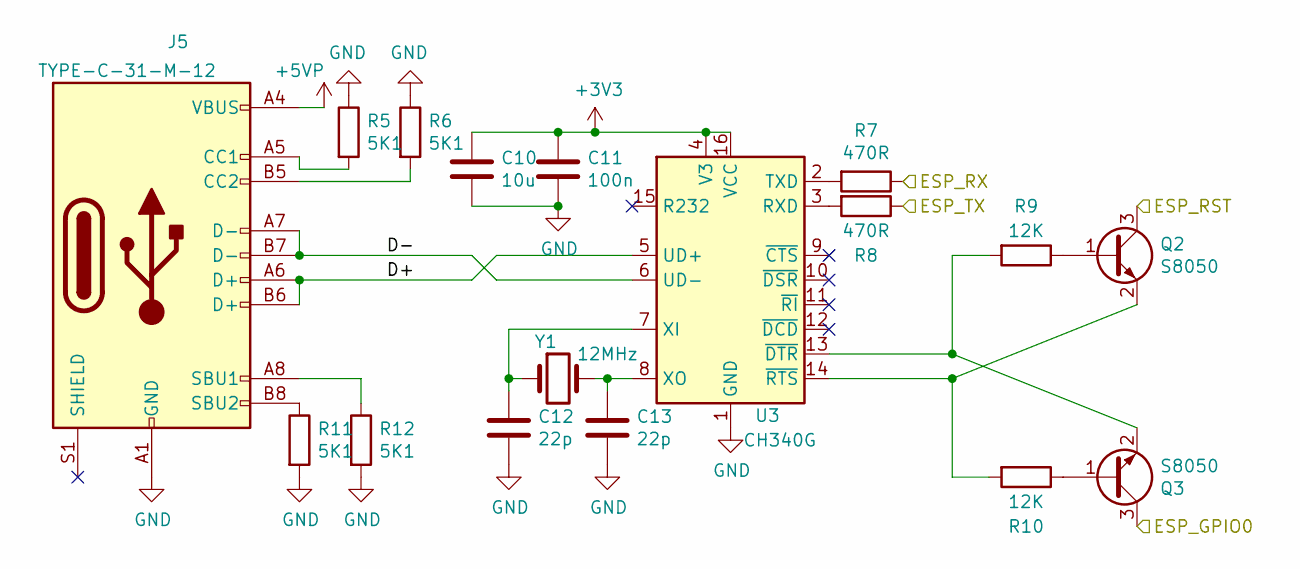
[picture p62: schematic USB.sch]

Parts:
C10: 10u; C_0805_2012Metric; LCSC C15850
C11: 100n; C_0603_1608Metric; LCSC C14663
C12, C13: 22p; C_0603_1608Metric; LCSC C1653
J5: TYPE-C-31-M-12; USB_C_Receptacle_HRO_TYPE-C-31-M-12; LCSC C165948
Q2, Q3: S8050; SOT-23; LCSC C2146
R5, R6, R11, R12: 5K1; R_0603_1608Metric; LCSC C23186
R7, R8: 470R; R_0603_1608Metric; LCSC C23179
R9, R10: 12K; R_0603_1608Metric; LCSC C22790
U3: CH340G; SOIC-16_3.9x9.9mm_P1.27mm; LCSC C14267
Y1: 12MHz; Crystal_HC49-4H_Vertical

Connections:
+3V3: C10.1, C11.1, U3.4 (V3), U3.16 (VCC); also elsewhere on the board
+5VP: J5.A4 (VBUS), J5.A9 (VBUS), J5.B4 (VBUS), J5.B9 (VBUS); also elsewhere on the board
/USB/D+: J5.A6 (D+), J5.B6 (D+), U3.5 (UD+)
/USB/D-: J5.A7 (D-), J5.B7 (D-), U3.6 (UD-)
/USB/ESP_GPIO0: Q3.3 (C); also elsewhere on the board
/USB/ESP_RST: Q2.3 (C); also elsewhere on the board
/USB/ESP_RX: R7.1; also elsewhere on the board
/USB/ESP_TX: R8.1; also elsewhere on the board
GND: C10.2, C11.2, C12.2, C13.2, J5.A1 (GND), J5.A12 (GND), J5.B1 (GND), J5.B12 (GND), R5.1, R6.1, R11.2, R12.2, U3.1 (GND); also elsewhere on the board
unnamed: C12.1, U3.7 (XI), Y1.1
unnamed: C13.1, U3.8 (XO), Y1.2
unnamed: J5.A5 (CC1), R5.2
unnamed: J5.A8 (SBU1), R12.1
unnamed: J5.B5 (CC2), R6.2
unnamed: J5.B8 (SBU2), R11.1
unnamed: Q2.1 (B), R9.1
unnamed: Q2.2 (E), R10.2, U3.14 (~RTS)
unnamed: Q3.1 (B), R10.1
unnamed: Q3.2 (E), R9.2, U3.13 (~DTR)
unnamed: R7.2, U3.2 (TXD)
unnamed: R8.2, U3.3 (RXD)

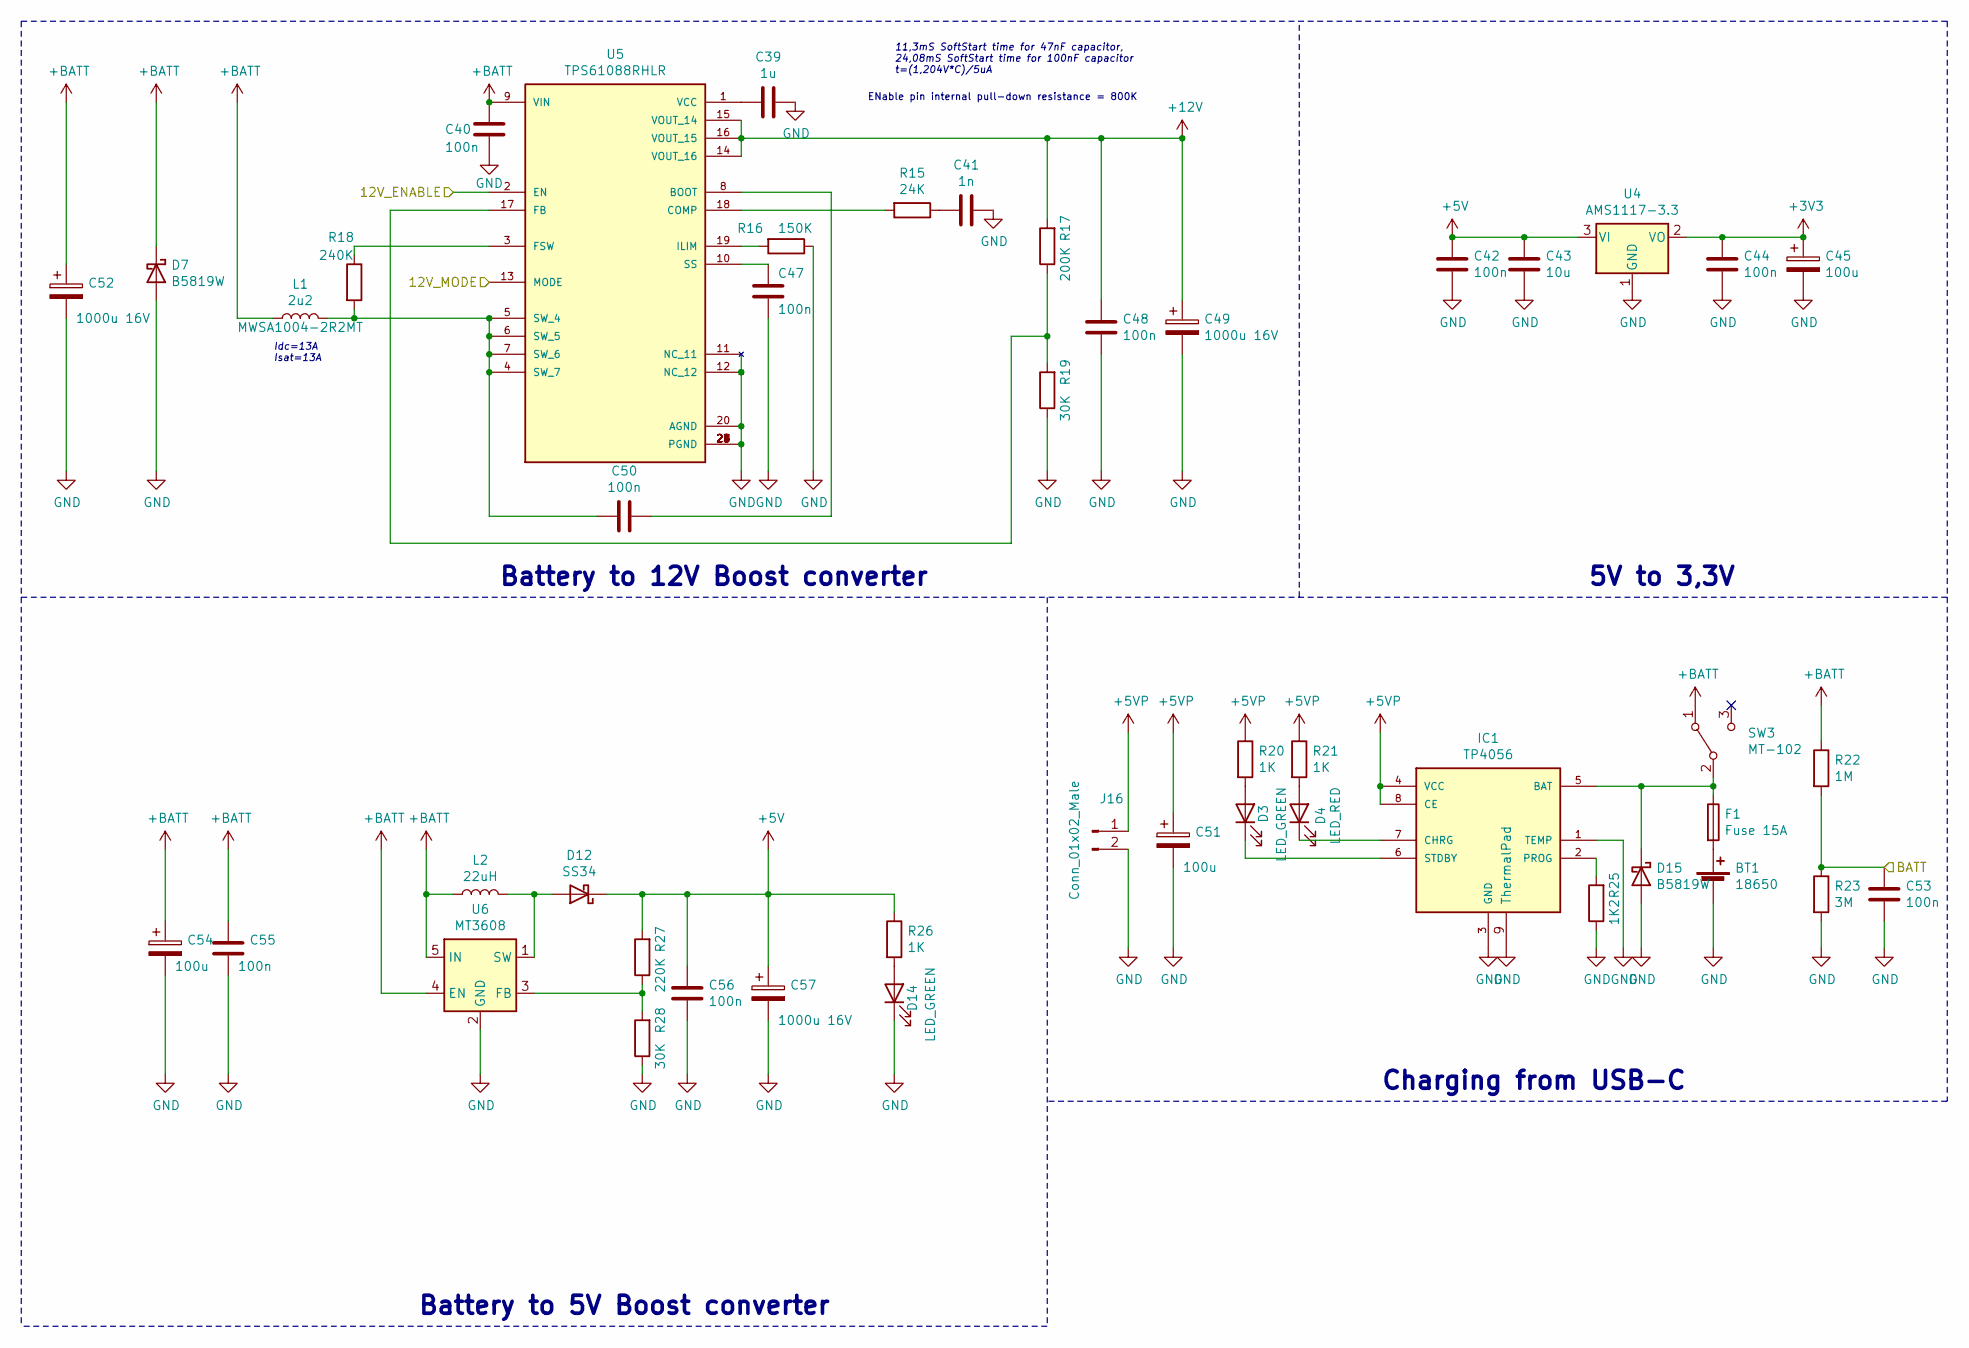
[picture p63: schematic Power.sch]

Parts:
BT1: 18650; BatteryHolder_MPD_BH-18650-PC2_NoHoles
C39: 1u; C_0603_1608Metric; LCSC C15849
C40, C42, C44, C47, C48, C50, C53, C55, C56: 100n; C_0603_1608Metric; LCSC C14663
C41: 1n; C_0603_1608Metric; LCSC C1588
C43: 10u; C_0805_2012Metric; LCSC C15850
C45, C51, C54: 100u; CP_Radial_D5.0mm_P2.00mm; LCSC C43803
C49, C52, C57: 1000u 16V; CP_Radial_D8.0mm_P3.50mm; LCSC C43348
D3, D14: LED_GREEN; LED_D3.0mm
D4: LED_RED; LED_D3.0mm
D7, D15: B5819W; D_SOD-123; LCSC C8598
D12: SS34; D_SMA; LCSC C8678
F1: Fuse 15A; Fuse_1206_3216Metric; LCSC C182976
IC1: TP4056; SOIC-8-1EP_3.9x4.9mm_P1.27mm_EP2.514x3.2mm_ThermalVias; LCSC C382139
J16: Conn_01x02_Male; PinHeader_1x02_P2.54mm_Vertical
L1: 2u2; L_Wuerth_HCI-1040; LCSC C149550
L2: 22uH; L_Wuerth_HCI-1040; LCSC C182173
R15: 24K; R_0603_1608Metric; LCSC C23352
R16: 150K; R_0603_1608Metric; LCSC C22807
R17: 200K; R_0603_1608Metric; LCSC C25811
R18: 240K; R_0603_1608Metric; LCSC C4197
R19, R28: 30K; R_0603_1608Metric; LCSC C22984
R20, R21, R26: 1K; R_0603_1608Metric; LCSC C21190
R22: 1M; R_0603_1608Metric; LCSC C22935
R23: 3M; R_0603_1608Metric; LCSC C23156
R25: 1K2; R_0603_1608Metric; LCSC C22765
R27: 220K; R_0603_1608Metric; LCSC C22961
SW3: MT-102; TE_A101SYCQ04
U4: AMS1117-3.3; SOT-223-3_TabPin2; LCSC C6186
U5: TPS61088RHLR; IC_TPS61088RHLR; LCSC C87357
U6: MT3608; SOT-23-6; LCSC C84817

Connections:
+3V3: C44.1, C45.1, U4.2 (VO); also elsewhere on the board
+5V: C42.1, C43.1, C56.1, C57.1, D12.1 (K), R26.1, R27.2, U4.3 (VI); also elsewhere on the board
+5VP: C51.1, IC1.4 (VCC), IC1.8 (CE), J16.1, R20.1, R21.1; also elsewhere on the board
+12V: C48.1, C49.1, R17.2, U5.14 (VOUT_16), U5.15 (VOUT_14), U5.16 (VOUT_15); also elsewhere on the board
+BATT: C40.1, C52.1, C54.1, C55.1, D7.1 (K), L1.1, L2.1, R22.1, SW3.1 (A), U5.9 (VIN), U6.4 (EN), U6.5 (IN)
/Mux Demux Matrix/Analog_IN_7: C53.1, R22.2, R23.1; also elsewhere on the board
/Power/12V_ENABLE: U5.2 (EN); also elsewhere on the board
/Power/12V_MODE: U5.13 (MODE); also elsewhere on the board
GND: BT1.2 (-), C39.1, C40.2, C41.1, C42.2, C43.2, C44.2, C45.2, C47.2, C48.2, C49.2, C51.2, C52.2, C53.2, C54.2, C55.2, C56.2, C57.2, D7.2 (A), D14.1 (K), D15.2 (A), IC1.1 (TEMP), IC1.3 (GND), IC1.9 (ThermalPad), J16.2, R16.1, R19.1, R23.2, R25.1, R28.1, U4.1 (GND), U5.11 (NC_11), U5.12 (NC_12), U5.20 (AGND), U5.21 (PGND), U5.22 (PGND), U5.23 (PGND), U5.24 (PGND), U5.25 (PGND), U5.26 (PGND), U5.27 (PGND), U5.28 (PGND), U5.29 (PGND), U6.2 (GND); also elsewhere on the board
unnamed: BT1.1 (+), F1.2
unnamed: C39.2, U5.1 (VCC)
unnamed: C41.2, R15.1
unnamed: C47.1, U5.10 (SS)
unnamed: C50.1, U5.8 (BOOT)
unnamed: C50.2, L1.2, R18.2, U5.4 (SW_7), U5.5 (SW_4), U5.6 (SW_5), U5.7 (SW_6)
unnamed: D3.1 (K), IC1.6 (STDBY)
unnamed: D3.2 (A), R20.2
unnamed: D4.1 (K), IC1.7 (CHRG)
unnamed: D4.2 (A), R21.2
unnamed: D12.2 (A), L2.2, U6.1 (SW)
unnamed: D14.2 (A), R26.2
unnamed: D15.1 (K), F1.1, IC1.5 (BAT), SW3.2 (B)
unnamed: IC1.2 (PROG), R25.2
unnamed: R15.2, U5.18 (COMP)
unnamed: R16.2, U5.19 (ILIM)
unnamed: R17.1, R19.2, U5.17 (FB)
unnamed: R18.1, U5.3 (FSW)
unnamed: R27.1, R28.2, U6.3 (FB)

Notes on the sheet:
11,3mS SoftStart time for 47nF capacitor, 24,08mS SoftStart time for 100nF capacitor t=(1,204V*C)/5uA
Idc=13A Isat=13A
ENable pin internal pull-down resistance = 800K
Battery to 12V Boost converter
5V to 3,3V
Battery to 5V Boost converter
Charging from USB-C

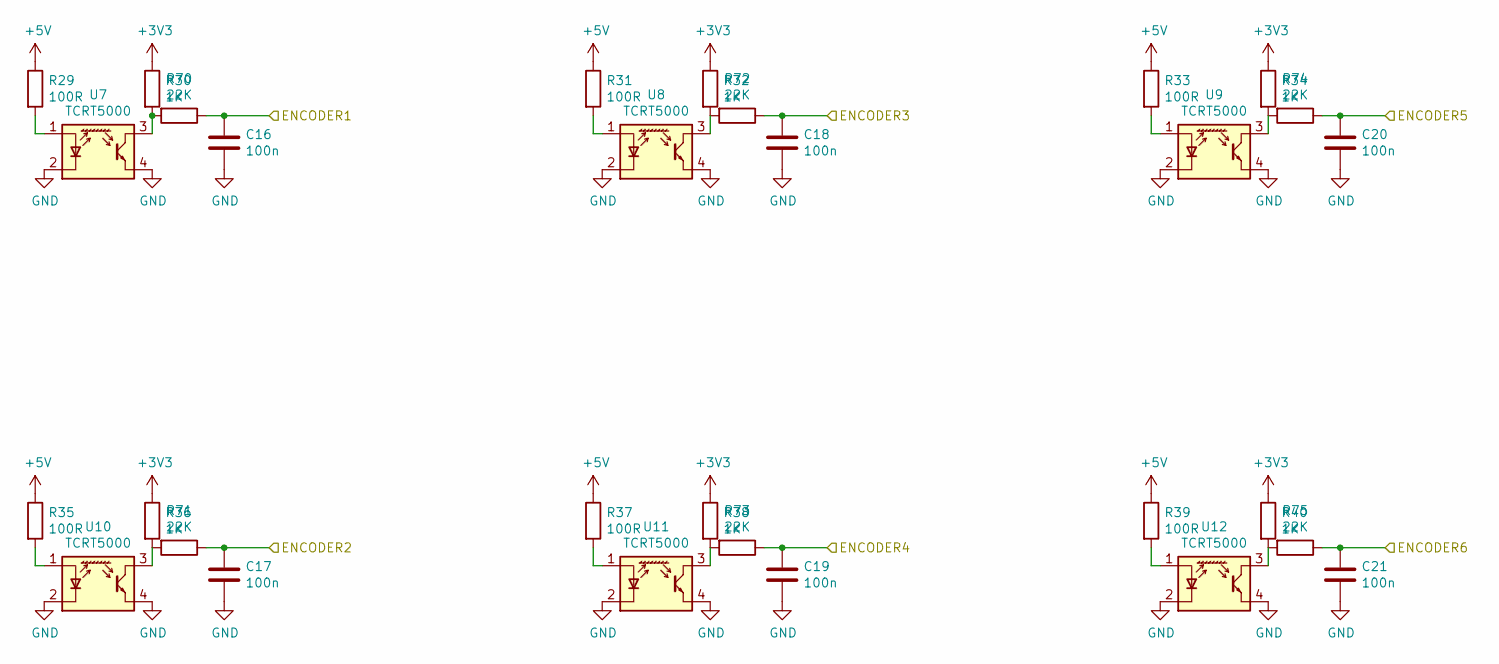
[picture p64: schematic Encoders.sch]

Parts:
C16, C17, C18, C19, C20, C21: 100n; C_0603_1608Metric; LCSC C14663
R29, R31, R33, R35, R37, R39: 100R; R_0805_2012Metric; LCSC C17408
R30, R32, R34, R36, R38, R40: 1K; R_0603_1608Metric; LCSC C21190
R70, R71, R72, R73, R74, R75: 22K; R_0603_1608Metric; LCSC C31850
U7, U8: TCRT5000
U9, U10, U11, U12: TCRT5000; TCRT5000_SMD

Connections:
+3V3: R30.1, R32.1, R34.1, R36.1, R38.1, R40.1; also elsewhere on the board
+5V: R29.1, R31.1, R33.1, R35.1, R37.1, R39.1; also elsewhere on the board
/Encoders/ENCODER2: C17.1, R71.1; also elsewhere on the board
/Encoders/ENCODER4: C19.1, R73.1; also elsewhere on the board
/Encoders/ENCODER5: C20.1, R74.1; also elsewhere on the board
/Encoders/ENCODER6: C21.1, R75.1; also elsewhere on the board
/Mux Demux Matrix/Analog_IN_1: C16.1, R70.1; also elsewhere on the board
/Mux Demux Matrix/Analog_IN_3: C18.1, R72.1; also elsewhere on the board
GND: C16.2, C17.2, C18.2, C19.2, C20.2, C21.2, U7.2 (K), U7.4 (E), U8.2 (K), U8.4 (E), U9.2 (K), U9.4 (E), U10.2 (K), U10.4 (E), U11.2 (K), U11.4 (E), U12.2 (K), U12.4 (E); also elsewhere on the board
unnamed: R29.2, U7.1 (A)
unnamed: R30.2, R70.2, U7.3 (C)
unnamed: R31.2, U8.1 (A)
unnamed: R32.2, R72.2, U8.3 (C)
unnamed: R33.2, U9.1 (A)
unnamed: R34.2, R74.2, U9.3 (C)
unnamed: R35.2, U10.1 (A)
unnamed: R36.2, R71.2, U10.3 (C)
unnamed: R37.2, U11.1 (A)
unnamed: R38.2, R73.2, U11.3 (C)
unnamed: R39.2, U12.1 (A)
unnamed: R40.2, R75.2, U12.3 (C)

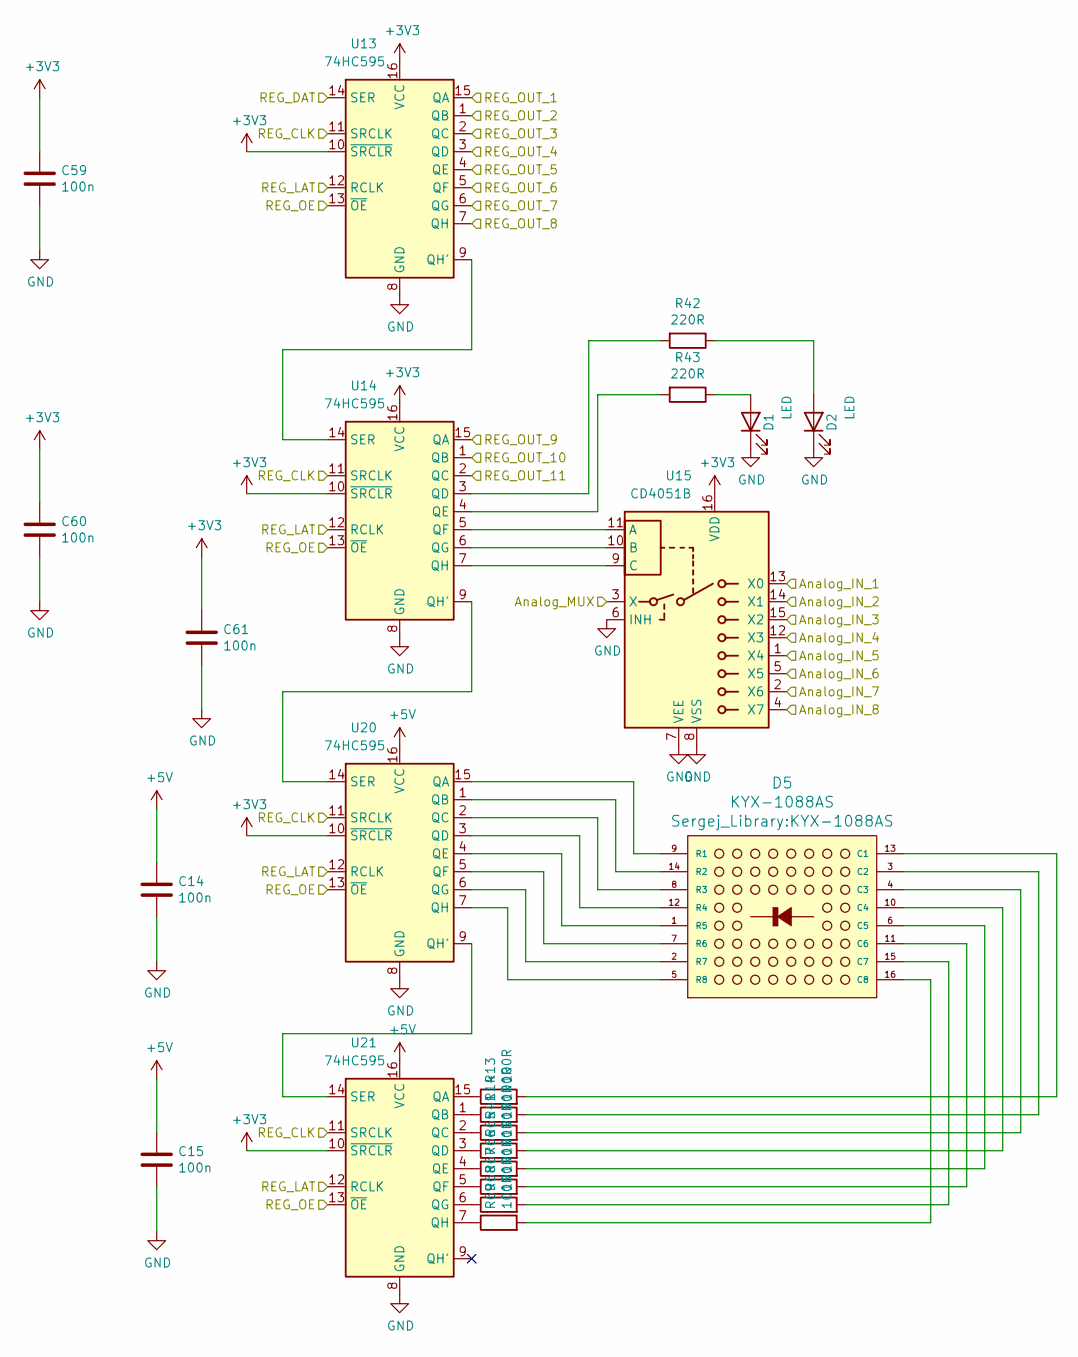
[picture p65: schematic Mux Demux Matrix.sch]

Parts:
C14, C15, C59, C60, C61: 100n; C_0603_1608Metric; LCSC C14663
D1, D2: LED; LED_D3.0mm
D5: KYX-1088AS
R13, R14, R41, R65, R66, R67, R68, R69: 100R; R_0805_2012Metric; LCSC C17408
R42, R43: 220R; R_0603_1608Metric; LCSC C22962
U13, U14, U20, U21: 74HC595; SOIC-16_3.9x9.9mm_P1.27mm; LCSC C5947
U15: CD4051B; SOIC-16_3.9x9.9mm_P1.27mm; LCSC C21379

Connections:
+3V3: C59.1, C60.1, C61.1, U13.10 (~SRCLR), U13.16 (VCC), U14.10 (~SRCLR), U14.16 (VCC), U15.16 (VDD), U20.10 (~SRCLR), U21.10 (~SRCLR); also elsewhere on the board
+5V: C14.1, C15.1, U20.16 (VCC), U21.16 (VCC); also elsewhere on the board
/Motors/DC_MOT1_12V: U13.6 (QG); also elsewhere on the board
/Motors/DC_MOT2_5V: U13.7 (QH); also elsewhere on the board
/Motors/DC_MOT3_12V: U14.15 (QA); also elsewhere on the board
/Motors/DC_MOT4_5V: U14.1 (QB); also elsewhere on the board
/Motors/MOTA_IN1: U13.15 (QA); also elsewhere on the board
/Motors/MOTA_IN2: U13.1 (QB); also elsewhere on the board
/Motors/MOTB_IN1: U13.2 (QC); also elsewhere on the board
/Motors/MOTB_IN2: U13.3 (QD); also elsewhere on the board
/Mux Demux Matrix/Analog_IN_1: U15.13 (X0); also elsewhere on the board
/Mux Demux Matrix/Analog_IN_3: U15.15 (X2); also elsewhere on the board
/Mux Demux Matrix/Analog_IN_4: U15.12 (X3); also elsewhere on the board
/Mux Demux Matrix/Analog_IN_5: U15.1 (X4); also elsewhere on the board
/Mux Demux Matrix/Analog_IN_6: U15.5 (X5); also elsewhere on the board
/Mux Demux Matrix/Analog_IN_7: U15.2 (X6); also elsewhere on the board
/Mux Demux Matrix/Analog_MUX: U15.3 (X); also elsewhere on the board
/Mux Demux Matrix/REG_CLK: U13.11 (SRCLK), U14.11 (SRCLK), U20.11 (SRCLK), U21.11 (SRCLK); also elsewhere on the board
/Mux Demux Matrix/REG_DAT: U13.14 (SER); also elsewhere on the board
/Mux Demux Matrix/REG_LAT: U13.12 (RCLK), U14.12 (RCLK), U20.12 (RCLK), U21.12 (RCLK); also elsewhere on the board
/Mux Demux Matrix/REG_OE: U13.13 (~OE), U14.13 (~OE), U20.13 (~OE), U21.13 (~OE); also elsewhere on the board
/Mux Demux Matrix/REG_OUT_11: U14.2 (QC); also elsewhere on the board
/Power/12V_ENABLE: U13.4 (QE); also elsewhere on the board
/Power/12V_MODE: U13.5 (QF); also elsewhere on the board
GND: C14.2, C15.2, C59.2, C60.2, C61.2, D1.1 (K), D2.1 (K), U13.8 (GND), U14.8 (GND), U15.6 (INH), U15.7 (VEE), U15.8 (VSS), U20.8 (GND), U21.8 (GND); also elsewhere on the board
unnamed: D1.2 (A), R43.1
unnamed: D2.2 (A), R42.1
unnamed: D5.1 (R5), U20.4 (QE)
unnamed: D5.2 (R7), U20.6 (QG)
unnamed: D5.3 (C2), R14.2
unnamed: D5.4 (C3), R41.2
unnamed: D5.5 (R8), U20.7 (QH)
unnamed: D5.6 (C5), R66.2
unnamed: D5.7 (R6), U20.5 (QF)
unnamed: D5.8 (R3), U20.2 (QC)
unnamed: D5.9 (R1), U20.15 (QA)
unnamed: D5.10 (C4), R65.2
unnamed: D5.11 (C6), R67.2
unnamed: D5.12 (R4), U20.3 (QD)
unnamed: D5.13 (C1), R13.2
unnamed: D5.14 (R2), U20.1 (QB)
unnamed: D5.15 (C7), R68.2
unnamed: D5.16 (C8), R69.2
unnamed: R13.1, U21.15 (QA)
unnamed: R14.1, U21.1 (QB)
unnamed: R41.1, U21.2 (QC)
unnamed: R42.2, U14.3 (QD)
unnamed: R43.2, U14.4 (QE)
unnamed: R65.1, U21.3 (QD)
unnamed: R66.1, U21.4 (QE)
unnamed: R67.1, U21.5 (QF)
unnamed: R68.1, U21.6 (QG)
unnamed: R69.1, U21.7 (QH)
unnamed: U13.9 (QH'), U14.14 (SER)
unnamed: U14.5 (QF), U15.11 (A)
unnamed: U14.6 (QG), U15.10 (B)
unnamed: U14.7 (QH), U15.9 (C)
unnamed: U14.9 (QH'), U20.14 (SER)
unnamed: U20.9 (QH'), U21.14 (SER)
POT: U15.4 (X7); also elsewhere on the board

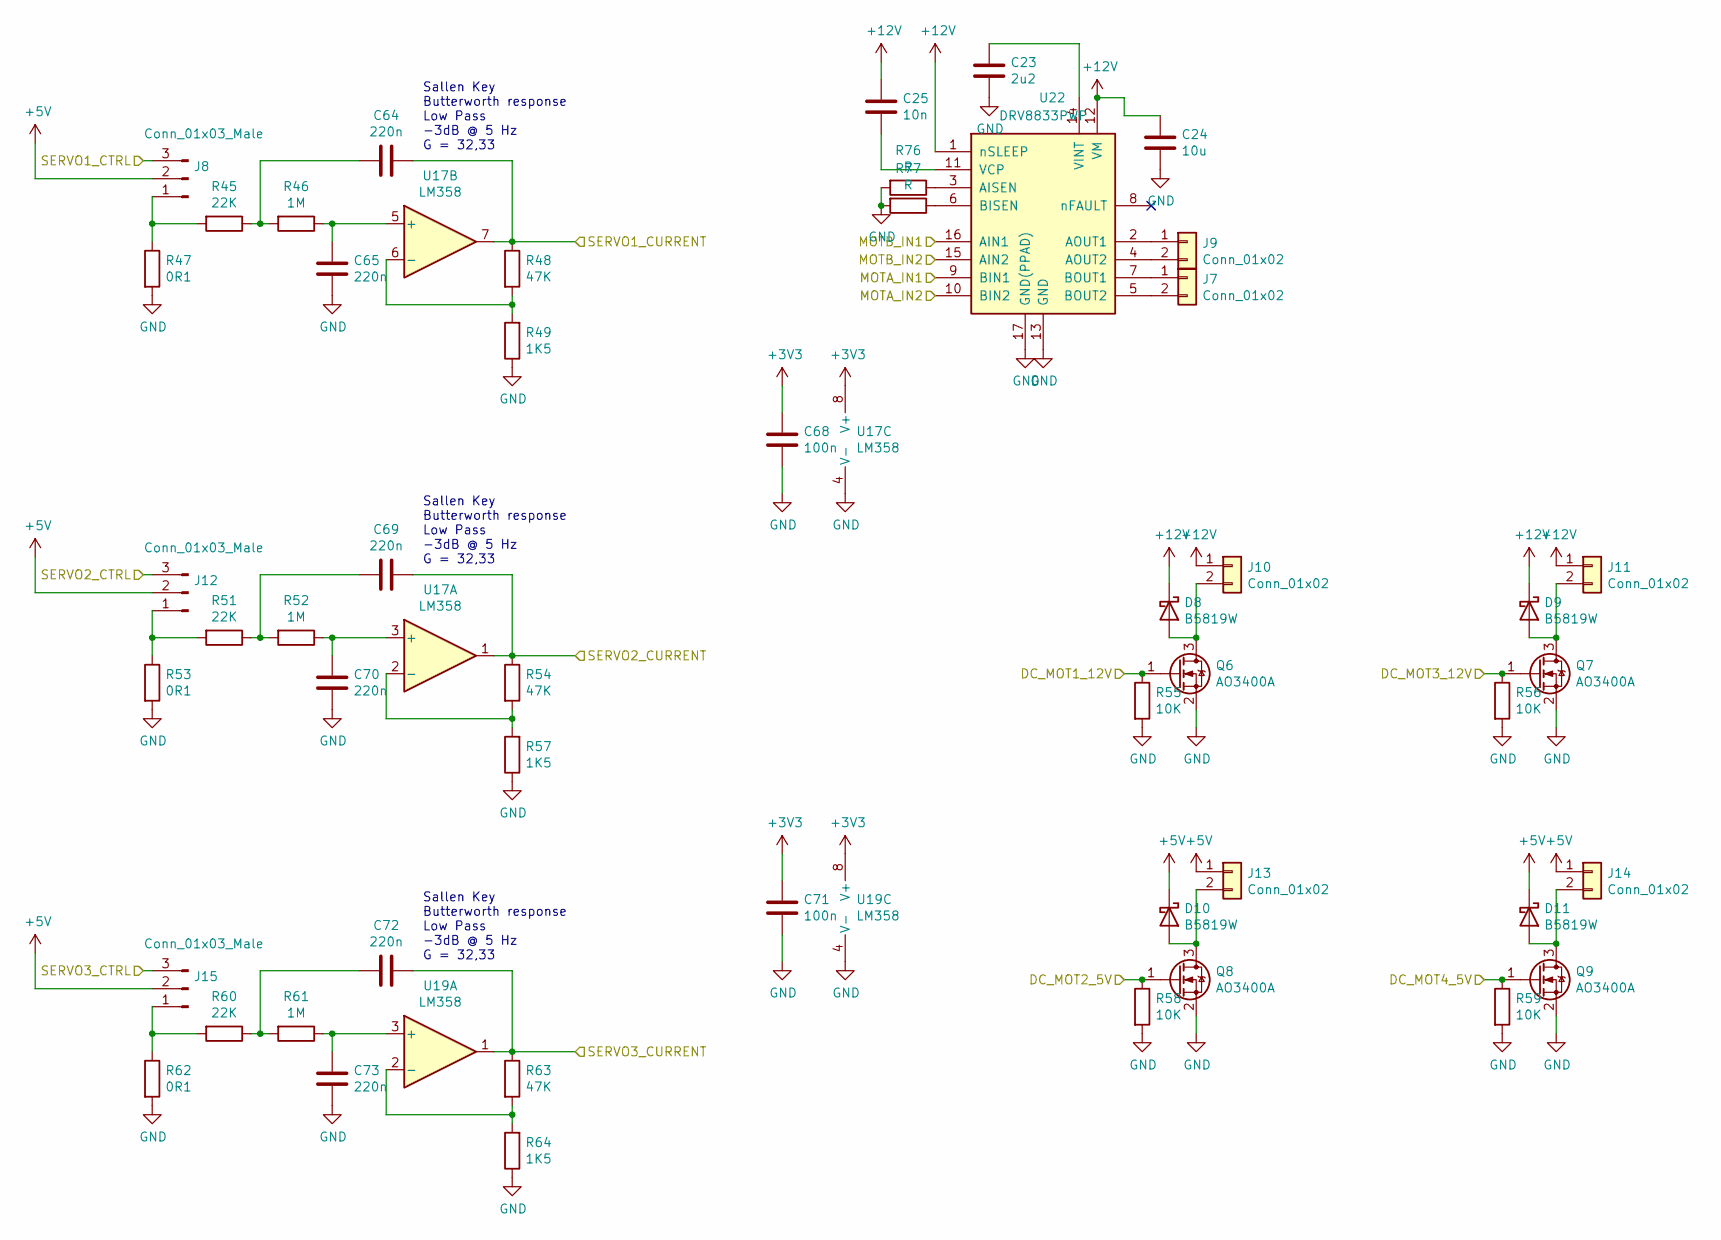
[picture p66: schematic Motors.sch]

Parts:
C23: 2u2; C_0603_1608Metric; LCSC C23630
C24: 10u; C_0805_2012Metric; LCSC C15850
C25: 10n; C_0603_1608Metric; LCSC C57112
C64, C65, C69, C70, C72, C73: 220n; C_0603_1608Metric; LCSC C21120
C68, C71: 100n; C_0603_1608Metric; LCSC C14663
D8, D9, D10, D11: B5819W; D_SOD-123; LCSC C8598
J7, J9, J10, J11, J13, J14: Conn_01x02; JST_XH_B2B-XH-A_1x02_P2.50mm_Vertical
J8, J12, J15: Conn_01x03_Male; PinHeader_1x03_P2.54mm_Vertical
Q6, Q7, Q8, Q9: AO3400A; SOT-23; LCSC C20917
R45, R51, R60: 22K; R_0603_1608Metric; LCSC C31850
R46, R52, R61: 1M; R_0603_1608Metric; LCSC C22935
R47, R53, R62: 0R1; R_1206_3216Metric; LCSC C25334
R48, R54, R63: 47K; R_0603_1608Metric; LCSC C25819
R49, R57, R64: 1K5; R_0603_1608Metric; LCSC C22843
R55, R56, R58, R59: 10K; R_0603_1608Metric; LCSC C25804
R76, R77: R; R_1206_3216Metric_Pad1.30x1.75mm_HandSolder
U17, U19: LM358; SOIC-8_3.9x4.9mm_P1.27mm; LCSC C7950
U22: DRV8833PWP; HTSSOP-16-1EP_4.4x5mm_P0.65mm_EP3.4x5mm_Mask2.46x2.31mm_The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

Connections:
+3V3: C68.1, C71.1, U17.8 (V+), U19.8 (V+); also elsewhere on the board
+5V: D10.1 (K), D11.1 (K), J8.2, J12.2, J13.1, J14.1, J15.2; also elsewhere on the board
+12V: C24.1, C25.1, D8.1 (K), D9.1 (K), J10.1, J11.1, U22.1 (nSLEEP), U22.12 (VM); also elsewhere on the board
/Motors/DC_MOT1_12V: Q6.1 (G), R55.1; also elsewhere on the board
/Motors/DC_MOT2_5V: Q8.1 (G), R58.1; also elsewhere on the board
/Motors/DC_MOT3_12V: Q7.1 (G), R56.1; also elsewhere on the board
/Motors/DC_MOT4_5V: Q9.1 (G), R59.1; also elsewhere on the board
/Motors/MOTA_IN1: U22.9 (BIN1); also elsewhere on the board
/Motors/MOTA_IN2: U22.10 (BIN2); also elsewhere on the board
/Motors/MOTB_IN1: U22.16 (AIN1); also elsewhere on the board
/Motors/MOTB_IN2: U22.15 (AIN2); also elsewhere on the board
/Motors/SERVO1_CTRL: J8.3; also elsewhere on the board
/Motors/SERVO2_CTRL: J12.3; also elsewhere on the board
/Motors/SERVO3_CTRL: J15.3; also elsewhere on the board
/Mux Demux Matrix/Analog_IN_4: C64.1, R48.1, U17.7; also elsewhere on the board
/Mux Demux Matrix/Analog_IN_5: C69.1, R54.1, U17.1; also elsewhere on the board
/Mux Demux Matrix/Analog_IN_6: C72.1, R63.1, U19.1; also elsewhere on the board
GND: C23.2, C24.2, C65.1, C68.2, C70.1, C71.2, C73.1, Q6.2 (S), Q7.2 (S), Q8.2 (S), Q9.2 (S), R47.2, R49.1, R53.2, R55.2, R56.2, R57.1, R58.2, R59.2, R62.2, R64.1, R76.2, R77.2, U17.4 (V-), U19.4 (V-), U22.13 (GND), U22.17 (GND(PPAD)); also elsewhere on the board
unnamed: C23.1, U22.14 (VINT)
unnamed: C25.2, U22.11 (VCP)
unnamed: C64.2, R45.1, R46.2
unnamed: C65.2, R46.1, U17.5 (+)
unnamed: C69.2, R51.1, R52.2
unnamed: C70.2, R52.1, U17.3 (+)
unnamed: C72.2, R60.1, R61.2
unnamed: C73.2, R61.1, U19.3 (+)
unnamed: D8.2 (A), J10.2, Q6.3 (D)
unnamed: D9.2 (A), J11.2, Q7.3 (D)
unnamed: D10.2 (A), J13.2, Q8.3 (D)
unnamed: D11.2 (A), J14.2, Q9.3 (D)
unnamed: J7.1, U22.7 (BOUT1)
unnamed: J7.2, U22.5 (BOUT2)
unnamed: J8.1, R45.2, R47.1
unnamed: J9.1, U22.2 (AOUT1)
unnamed: J9.2, U22.4 (AOUT2)
unnamed: J12.1, R51.2, R53.1
unnamed: J15.1, R60.2, R62.1
unnamed: R48.2, R49.2, U17.6 (-)
unnamed: R54.2, R57.2, U17.2 (-)
unnamed: R63.2, R64.2, U19.2 (-)
unnamed: R76.1, U22.3 (AISEN)
unnamed: R77.1, U22.6 (BISEN)

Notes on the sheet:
Sallen Key Butterworth response Low Pass -3dB @ 5 Hz G = 32,33

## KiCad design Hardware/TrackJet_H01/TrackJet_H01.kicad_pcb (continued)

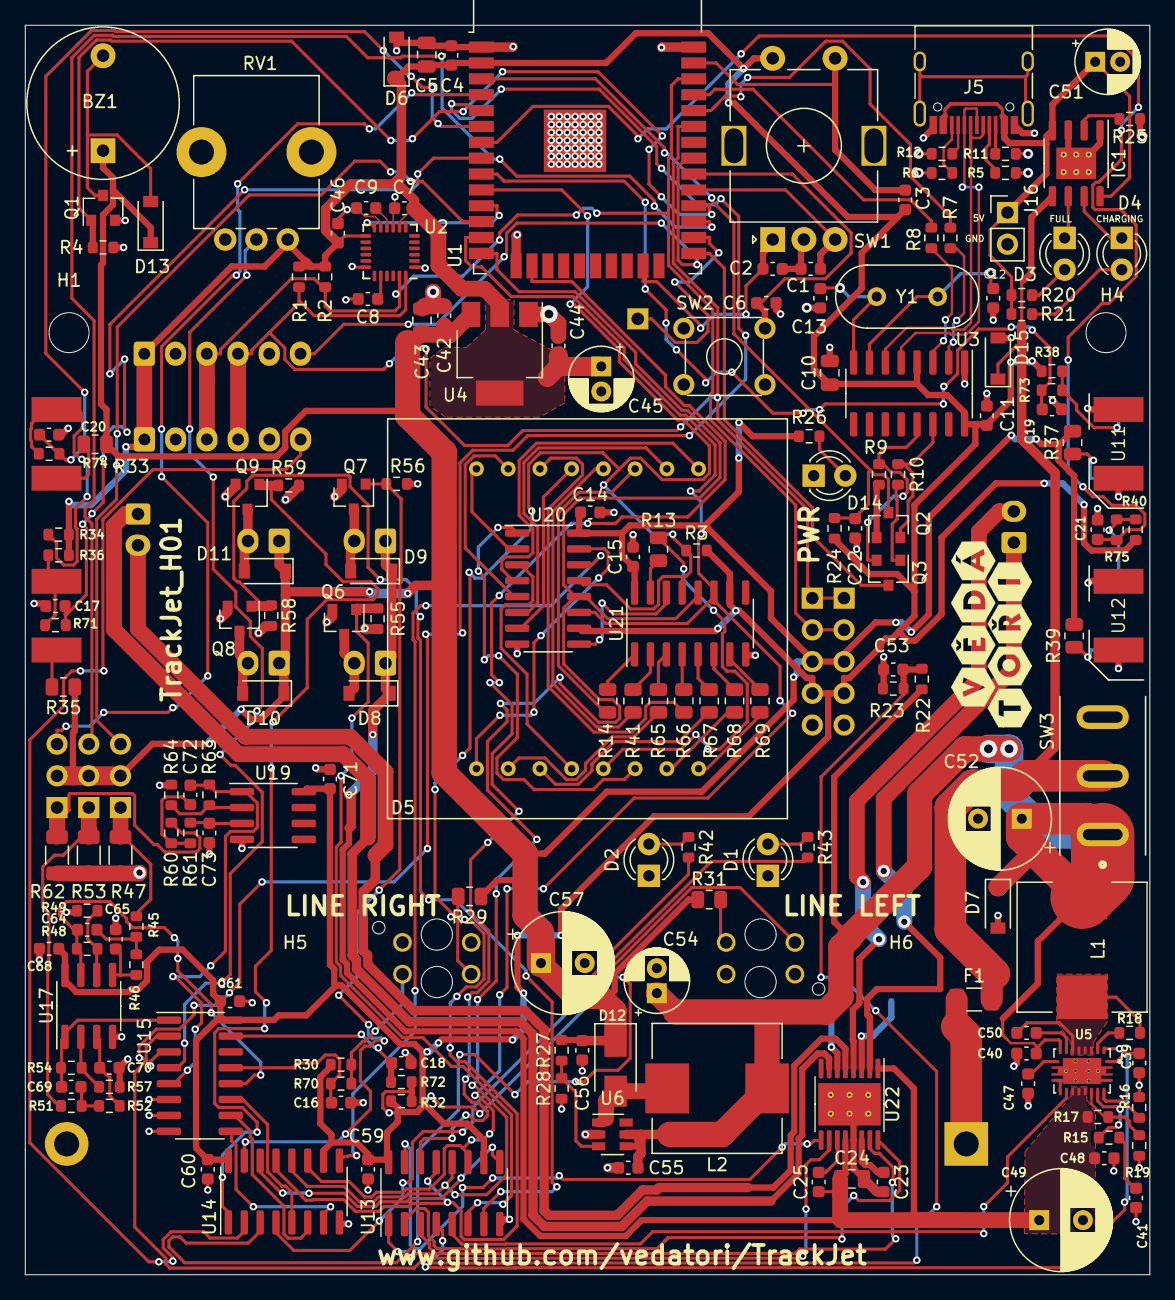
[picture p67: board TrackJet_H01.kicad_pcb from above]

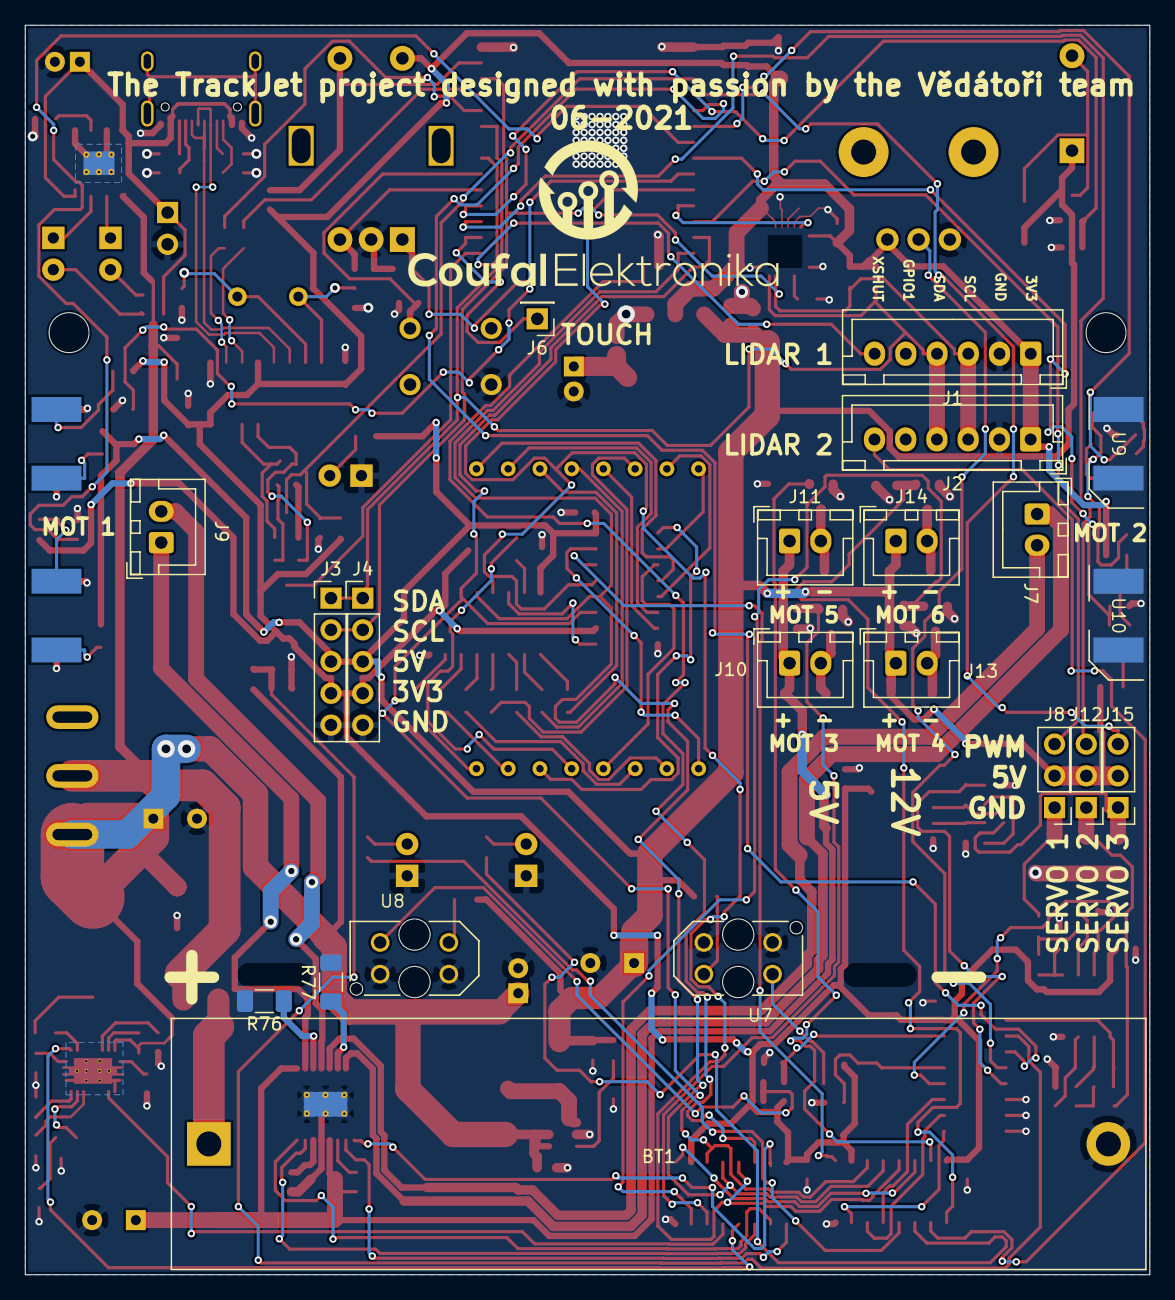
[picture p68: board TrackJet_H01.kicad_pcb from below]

Board: 2 copper layers, 90.0 x 100.0 mm, 205 parts (22 on the bottom side), 156 nets.

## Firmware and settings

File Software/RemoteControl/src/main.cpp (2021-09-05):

#include "TrackJet/TrackJet.h"

const uint8_t CONTROL_PERIOD = 100;
uint32_t prevControlTime = 0;

void setup() {
    TrackJet.begin();
    TrackJet.startWiFiCaptain("<your_name>");
    TrackJet.displayText(ipToDisp());
    TrackJet.servoSetSpeed(1, 60);
}

void loop() {
    if(millis() > prevControlTime + CONTROL_PERIOD) {
        prevControlTime = millis();
        if(TrackJet.displayIsBusy() == false) {
            TrackJet.displayDigit(TrackJet.encoderRead()%10);
            for(uint8_t i = 0; i < 8; ++i) {
                TrackJet.displaySingle(i, 7, 0);
                TrackJet.displaySingle(i, 6, 0);
            }
            for(uint8_t i = 0; i < TrackJet.battPercent()/12; ++i) {
                TrackJet.displaySingle(7 - i, 7, 1);
            }
            TrackJet.displaySingle(TrackJet.lidarDistance()/100, 6, 1);
        }

        if(TrackJet.commandGetIndexed(0) == "blade") {
            TrackJet.servoSetPosition(1, TrackJet.commandGetIndexed(1).toInt());
            TrackJet.commandClear();
        }
        else if(TrackJet.commandGetIndexed(0) == "head") {
            TrackJet.servoSetPosition(2, TrackJet.commandGetIndexed(1).toInt());
            TrackJet.commandClear();
        }
        else if(TrackJet.commandGetIndexed(0) == "beep") {
            TrackJet.soundTone();
            delay(500);
            TrackJet.soundEnd();
            TrackJet.commandClear();
        }
        else if(TrackJet.commandGet() == "take on me") {
            TrackJet.playMelody(takeonme, sizeof(takeonme), takeonme_tempo);
            TrackJet.commandClear();
        }
        else if(TrackJet.commandGetIndexed(0) == "silence") {
            TrackJet.stopMelody();
            TrackJet.commandClear();
        }
    }
}

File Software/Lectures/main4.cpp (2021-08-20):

// Lekce 4 - roztočíme motory a ukážeme si podmínku "if"
#include "TrackJet/TrackJet.h"

void setup() {
    TrackJet.begin();
	
	// Roztočení motoru 0 (levý pás) na 50% výkonu
	TrackJet.motorsSetSpeed(1, 50);
	delay(1000);
}

void loop() {
    if(TrackJet.buttonRead()) {
		// Když je tláčítko zmáčknuto, roztočí se oba motory
		TrackJet.motorsSetSpeed(1, 50);
		TrackJet.motorsSetSpeed(2, 50);
	}
	else {
		// Když není tláčítko zmáčknuto, oba motory se zastaví
		TrackJet.motorsSetSpeed(1, 0);
		TrackJet.motorsSetSpeed(2, 0);
	}

    delay(100);
}

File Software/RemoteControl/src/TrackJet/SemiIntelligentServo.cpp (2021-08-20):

#include <Arduino.h>

#include "SemiIntelligentServo.h"

SemiIntelligentServo::SemiIntelligentServo(uint8_t aPwmPin, uint8_t aPwmChannel) {
    pwmPin = aPwmPin;
    pwmChannel = aPwmChannel;
    ledcSetup(pwmChannel, servoFreqPWM, servoResolPWM);
    ledcAttachPin(pwmPin, pwmChannel);
    speed = 600;            // default speed
    targetAchieved = true;  // at start stay in original position by not sending PWM
    currentPosition = 90;   // initial servo moving position
    targetPosition = 90;
    prevUpdateTime = 0;
}
void SemiIntelligentServo::setPWM(float aPosition) {
    if(aPosition < 0)
        aPosition = 0;
    else if(aPosition > 180)
        aPosition = 180;
    uint16_t dutyCycleServo = aPosition/180*(servoCountHigh - servoCountLow) + servoCountLow;
    ledcWrite(pwmChannel, dutyCycleServo);
}
void SemiIntelligentServo::setPosition(float aPosition) {
    if(aPosition < 0)
        aPosition = 0;
    else if(aPosition > 180)
        aPosition = 180;
    targetPosition = aPosition;
    targetAchieved = false;
}
float SemiIntelligentServo::getPosition() {
    return currentPosition;
}
bool SemiIntelligentServo::moving() {
    return !targetAchieved;
}
void SemiIntelligentServo::setSpeed(float aSpeed) {
    if(aSpeed < 0)
        aSpeed = 0;
    else if(aSpeed > 600)
        aSpeed = 600;
    speed = aSpeed;
}
void SemiIntelligentServo::updatePWM() {
    
    float step = speed*(millis() - prevUpdateTime)/1000.0;
    if(targetPosition > currentPosition + step)
        currentPosition = currentPosition + step;
    else if(targetPosition < currentPosition - step)
        currentPosition = currentPosition - step;
    else
        currentPosition = targetPosition;
    
    if(targetAchieved == false)
        setPWM(currentPosition);
    if(currentPosition == targetPosition)
        targetAchieved = true;
    

    prevUpdateTime = millis();
}

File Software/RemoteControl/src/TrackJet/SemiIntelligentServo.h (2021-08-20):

#ifndef _SEMI_INTELLIGENT_SERVO_H_
#define _SEMI_INTELLIGENT_SERVO_H_

#include <Arduino.h>

class SemiIntelligentServo {
    static const uint8_t servoFreqPWM = 50;
    static const uint8_t servoResolPWM = 16;
    static const uint16_t servoCountLow = 1300; //1707
    static const uint16_t servoCountHigh = 8187;
    uint8_t pwmPin;
    uint8_t pwmChannel;
    float currentPosition;
    float targetPosition;
    float speed;
    bool targetAchieved;
    uint32_t prevUpdateTime;

public:
    SemiIntelligentServo(uint8_t aPwmPin, uint8_t aPwmChannel);
    void setPWM(float aPosition);
    void setPosition(float aPosition);
    float getPosition();
    bool moving();
    void setSpeed(float aSpeed);
    void updatePWM();
};

#endif  // _SEMI_INTELLIGENT_SERVO_H_

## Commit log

2021-03-19 Added first Hardware prototype.
    [18650_case_batt.step, Encoders.sch, Gyro.sch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]
2021-03-22 Routed PCB
    [Sergej_H00.dsn, Sergej_H00.kicad_pcb, Sergej_H00_batch1.kicad_pcb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]
2021-03-23 Final changes made to Sergej_H00, exported gerbers
    [Sergej_H00-B_Cu.gbr, Sergej_H00-B_Mask.gbr, Sergej_H00-B_Paste.gbr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]
2021-03-23 updated schematics - part values and LCSC numbers
    [Motors.sch, Mux Demux Matrix.sch, Power.sch]
2021-04-22 Notes for H01 and electronics analysis.
    [BOM.xlsx, Centroid.xlsx, Sergej_H00.kicad_pcb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]
2021-04-29 exported layout in PDF
    [Sergej_H00.kicad_pcb]
2021-05-14 Removed [ ] pwm operator.
2021-05-15 ShiftReg pin mapping and Handling OE pin in class.
2021-05-17 Fixed diplay orientation. Simple serialPWM disp api.
    [SerialPWM.cpp, SerialPWM.h, main.cpp]
2021-05-18 Added quadratic encoder.
2021-05-22 Controlling servos (+remotely through commands).
2021-05-22 Created TrackJet_H01
    Created TrackJet_H01 KiCad project and ported H00 version. Updated To-Do list. Renamed all files to TrackJet_Hxx except Sergej Library for compatibiliti with used symbols and footprints.
    [18650_case_batt.step, Encoders.sch, Gyro.sch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]
2021-05-22 Introduced servo class.
2021-05-22 Added speed adjustment of servos.
2021-05-23 Added MPU6050_light and reading YPR, calibrating and storing gyro calibration.
2021-05-23 Storing accelerometer calibration.
2021-05-24 Added lidar.
2021-06-11 Updated H01 PCB
    [Encoders.sch, Motors.sch, Power.sch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]
2021-06-13 Updated H01
    [TrackJet_H01.kicad_pcb]
2021-06-13 Lidar measurements with defined period
2021-06-14 H01 update
    [TrackJet_H01.dsn, TrackJet_H01.kicad_pcb]
2021-06-14 Exported H01 manufactuirng data
    [BOM.xlsx, Centroid.xlsx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]
2021-06-14 Updated manufacturing data
    [BOM.xlsx, Centroid.xlsx, Centroid2.xlsx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]
2021-07-11 Transition to H01. Added tracks encoder demo. Remove servo steady movement because of a bug.
    [SemiIntelligentServo.h, TrackJet.cpp, TrackJet.h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]
2021-08-08 Fixed lib naming issues with mac. Pinned updatePWM task to core 1 (same as main)
    [TrackJet.cpp, WiFiCaptain.cpp, main.cpp]
2021-08-08 Fixed WiFi softAp name conflict. Removed default password.
    [TrackJet.cpp, TrackJet.h, WiFiCaptain.cpp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]
2021-08-10 Reading analog mux inputs. Monitoring battery voltage.
2021-08-10 Gyro preferences loading only when gyro connected.
2021-08-12 Handling intern control commands (reset).
    [TrackJet.cpp, TrackJet.h, main.cpp]
2021-08-12 Fixed servo linear movement
    [SemiIntelligentServo.cpp, SemiIntelligentServo.h, TrackJet.cpp]
2021-08-12 Fixed servo commands calling. Added command entry autofocus.
    [main.cpp]
2021-08-12 Updated API for LED control. Prog.manual till buttons.
2021-08-12 Added second encoder monitoring.
2021-08-12 Encoder calibration
2021-08-14 programming lectures update
    button
2021-08-14 Fixed encoder threshold setup and calibration
    [TrackJet.cpp, main.cpp]
2021-08-14 Fixed encoder threshold storing.
    [TrackJet.cpp]
2021-08-15 Changed LED colors and indexes.
    [BOM.xlsx]
2021-08-16 Changed Push button index.
2021-08-16 Additional motors controlled. Renamed motors according to silk. Removed track motors speed filter.
2021-08-16 Updated motor api. Converted present sections of prog manual to TJ.
2021-08-17 Prog. tutorial + encoders api.
2021-08-17 Shows battery status in web-app
2021-08-17 Batt low voltage protection
2021-08-18 Battery voltage and info page
2021-08-18 Battery Status and Voltage merged to one message
2021-08-19 Fixed servo indexing. Fixed led manual.
    [TrackJet.cpp, TrackJet.h, main.cpp]
2021-08-19 Revert "Merge remote-tracking branch 'upstream/main' into main"
    This reverts commit 799921f37bc3124c14d1da9550b28997574ff44a, reversing
    changes made to 96676f5f47c76c1b3b095ec85f2c349d8c1f7739.
    [TrackJet.cpp, TrackJet.h, main.cpp]
2021-08-19 Revert "Revert "Merge remote-tracking branch 'upstream/main' into main""
    This reverts commit 10d234321a322cb9415ec9e53135bcc0bd4bd068.
    [TrackJet.cpp, TrackJet.h, main.cpp]
2021-08-19 Added functions for servo current position and movement.
2021-08-20 Encoder reset function

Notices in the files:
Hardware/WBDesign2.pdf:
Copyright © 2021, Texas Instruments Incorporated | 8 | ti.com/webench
